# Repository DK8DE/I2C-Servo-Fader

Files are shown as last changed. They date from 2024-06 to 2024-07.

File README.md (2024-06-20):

# I2C-Servo-Fader 
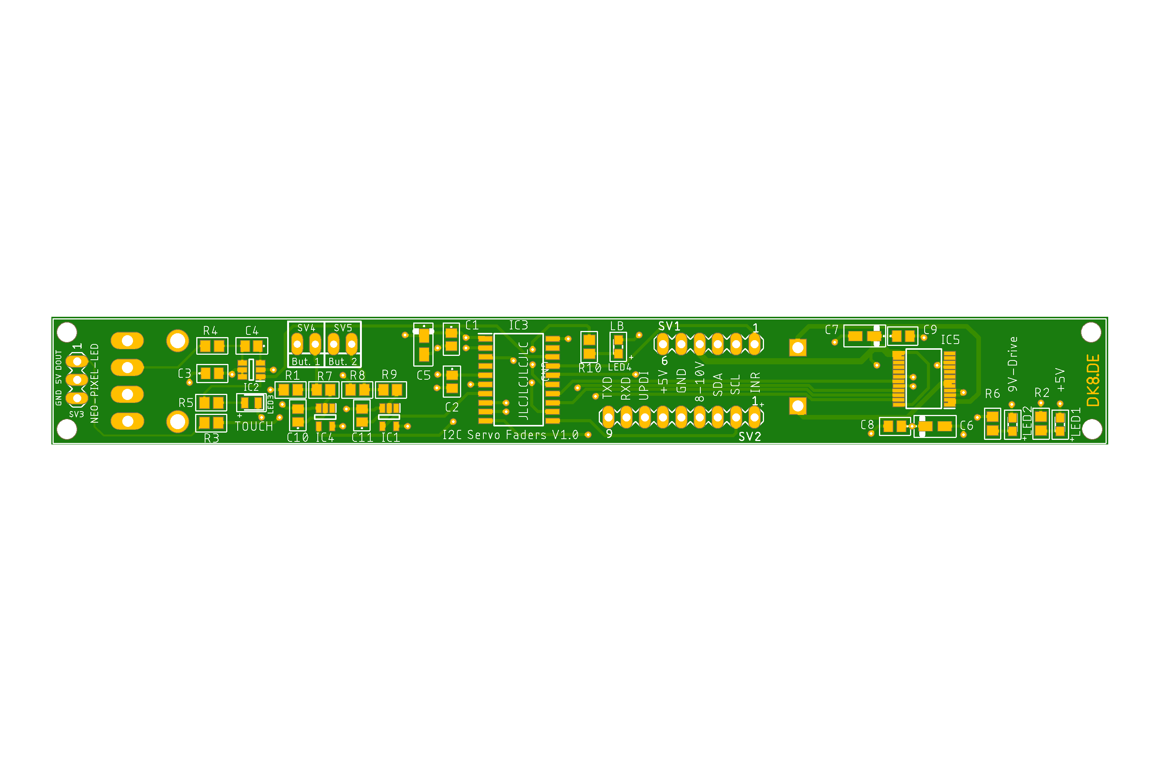
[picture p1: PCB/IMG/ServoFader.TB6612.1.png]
PCB

> [!CAUTION]
> The project is not yet complete. I am still waiting for the faders and the PCBs. Only then can I finish writing the code for the fader. The code still lacks the motor control in relation to the fader track.
## Description
This project consists of a board for a motor fader, the code for the microcontroller on the board, and a library to control this fader with an Arduino or an ESP32. The compatible faders are:
+ Behringer X-Touch Motor-Fader MF100T
+ Soundwell SM10001NKA0X-HA1
+ RSA0N11M9A07

Of course, the board can also be adapted for other faders by adjusting the footprint.

### Connections on the Board:
* SDA
* SCL
* +5V for the microcontroller
* 8-10V for the motor
* 1x interrupt pin
* 1x Opt button
* 1x Neo-Pixel-LED
* 1x UPDI

All signals are looped through on the board. This means that several boards can be placed next to each other and easily connected to each other.

## Funktion
The board also has the option to control a NeoPixel LED and an additional button. The NeoPixel LED can be fully controlled via the I2C bus, including RGB color, on, off, and brightness. This allows, for example, changing the color based on the set level or displaying notifications.
The fader has a touch function that can also be evaluated and is internally used to trigger an interrupt. You only need to check when the interrupt line is pulled LOW.
The optional button input can be queried and also triggers an interrupt when pressed.
The interrupt is only reset when the value on the fader that caused the interrupt is read. This ensures that no unnecessary queries are made and no changes are lost.
In the example code, the interrupt line is connected to a pin on the microcontroller that can also trigger an interrupt. This ensures that the microcontroller responds immediately to changes. On an Arduino UNO or Nano, pins 2 and 3 can be used.
To set an I2C address for the fader, you need to connect to the fader using the serial console and simply enter the address in the format 0x08. The address is then stored in ROM and used on the next startup. In theory, you can operate 127 faders on one bus ;-).
The functions of the library are thoroughly documented in I2cServoFader.h, and all functions are used in the example code. The example code also shows how to control multiple sliders.

# Example Code Description
This example code demonstrates how to control I2C servo sliders using an Arduino. The code supports one slider and can be extended to two sliders by uncommenting the relevant sections. The sliders can be controlled via serial commands, and their positions and LED colors can be adjusted based on analog values.

### Serial Commands:
+ sliderpos1=<value>: Sets the position of slider 1 to the specified value (0-255).
+ sliderpos2=<value>: Sets the position of slider 2 to the specified value (0-255).
+ slidertest=1: Initiates a demonstration of slider 1's movement through a series of positions.
+ slidertest=2: Initiates a demonstration of slider 2's movement through a series of positions.

### Interrupt Handling:
When an interrupt occurs, the code reads the analog value and optio state from the sliders, prints these values to the serial console, and updates the LED colors based on the analog values.
The interrupt is triggered by a change in the state of the connected pin (e.g., pin 2).

### LED Color Representation:
+ Green (analog value = 0)
+ Yellow (analog value ≈ 128)
+ Red (analog value = 255)
The LED color transitions smoothly between these values based on the analog value.
# Sources
Part of the circuit board layout is from this project:
https://github.com/GadgetReboot/PSM60_Fader_Controller

# Partlist
This is the BOM. If you don't buy the faders in Germany but from the friendly Chinese, they cost about 12€ per piece.
You can find them on AliExpress here: [RSA0N11M9A0J](https://de.aliexpress.com/item/1005006910254678.html).

| Part | Value | Package | PART_NUMBER | Price €|
|:--- |:--- |:--- |:--- |:--- |
| C1 | 100nF | C0805 | C0805C104K1RACTU | 0.16 | 
| C2 | 10nF | C0805 | C0805Y103K4RACTU | 0.16 |
| C3 | 100nF | C0805 | C0805C104K1RACTU | 0.16 |
| C4 | 22nF | C0805 | C0805C223K5RAC7210 | 0.09|
| C5 | 10uF | T491A | T491A106M016AT7280 | 0.35 |
| C6 | 10uF | T491A | T491A106M016AT7280 | 0.35 |
| C7 | 10uF | T491A | T491A106M016AT7280 | 0.35 |
| C8 | 100nF | C0805 | C0805C104K1RACTU | 0.16 |
| C9 | 100nF | C0805 | C0805C104K1RACTU | 0.16 |
| FADER | MF100T | SM10001NKA0X-HA1 |  | 20.00|
| IC1 | ATTINY1604-SSN | SOIC127P600X175-14N | ATTINY1604-SSN | 0.70|
| IC2 | AT42QT1010 | SOT95P280X145-6N | AT42QT1010-TSHR | 0.72|
| IC4 | SN74LVC1G14DBVR | SOT95P280X145-5N | SN74LVC1G14DBVR | 0.20 |
| IC5 | TB6612FNG,C,8,EL | SOP65P760X160-24N | TB6612FNG,C,8,EL | 1.35 |
| LED1 | 150080GS75000 | LEDM2012X80N | 150080GS75000 | 0.18 |
| LED2 | 150080GS75000 | LEDM2012X80N | 150080GS75000 | 0.18 |
| LED3 | 150080YS75000 | LEDC2012X80N | 150080YS75000 | 0.18 |
| R1 | 0R | R0805 | OPT | 0.08 |
| R2 | 1K | R0805 | | 0.08 |
| R3 | 470R | R0805 | | 0.08 | 
| R4 | 10K | R0805 | | 0.08 |
| R5 | 1K | R0805 | | 0.08 |
| R6 | 1K | R0805 | | 0.08 |
| SV1 | 0 | MA06-1 | | 0.15 |
| SV2 | 0 | MA06-1 | | 0.15 |
| SV3 | 0 | MA03-1 | | 0.15 |
| SV4 | 0 | MA03-1 | | 0.15 |
| SV5 | 22-23-2021 | 22-23-2021 | | 0.20 |
| PCB ||||2.00|
|T-Lever |||| 1.25 |
|Total |||| ~ 28.00€ |

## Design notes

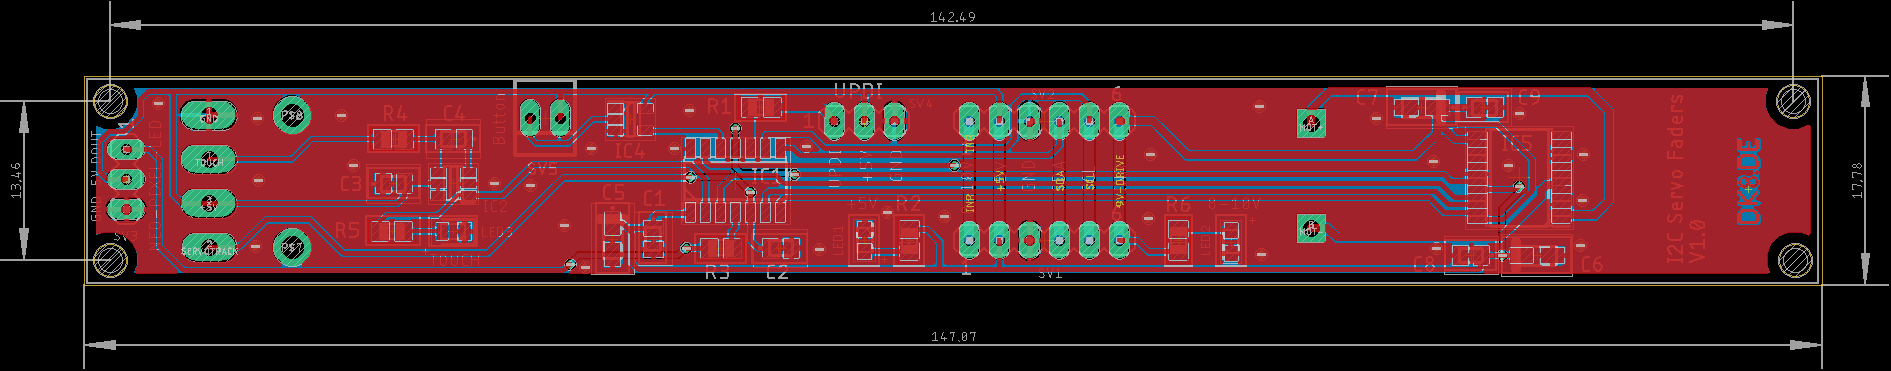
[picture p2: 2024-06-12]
PCB/IMG/ServoFader.TB6612.2.png

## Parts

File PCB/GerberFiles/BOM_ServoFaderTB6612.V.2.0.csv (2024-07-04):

Part | Value | Device | Package | Description | DESCRIPTION | HEIGHT | MANUFACTURER_NAME | MANUFACTURER_PART_NUMBER | MF | MOUSER_PART_NUMBER | MOUSER_PRICE-STOCK | MPN | OC_FARNELL | OC_NEWARK | POPULARITY | SPICEPREFIX
C1 | 100nF | C0805C104K1RACTU | C0805 | SMD Comm X7R, Ceramic, 0.1 uF, 10%, 100 VDC, 250 VDC, 125C, -55C, X7R, SMD, MLCC, Temperature Stable, Class II, 2.5 % , 10 GOhms, 16 mg, 0805, 2mm, 1.25mm, 1mm, 0.75mm, 0.5mm, 2500, 78 Weeks, 80 | SMD Comm X7R, Ceramic, 0.1 uF, 10%, 100 VDC, 250 VDC, 125C, -55C, X7R, SMD, MLCC, Temperature Stable, Class II, 2.5 % , 10 GOhms, 16 mg, 0805, 2mm, 1.25mm, 1mm, 0.75mm, 0.5mm, 2500, 78 Weeks, 80 | 1.1mm | KEMET | C0805C104K1RACTU |  | 80-C0805C104K1R | https://www.mouser.co.uk/ProductDetail/KEMET/C0805C104K1RACTU?qs=%252BnQd%252BVdkwTpk7hSy9esUqA%3D%3D
C2 | 10nF | C0805Y103K4RACTU | C0805 | SMD Comm X7R FF, Ceramic, 0.01 uF, 10%, 16 VDC, 40 VDC, 125C, -55C, X7R, SMD, MLCC, FF-CAP, Floating Electrode, 3.5 % , 100 GOhms, 13 mg, 0805, 2mm, 1.25mm, 0.78mm, 0.75mm, 0.5mm, 4000, 78 Weeks, 80 | SMD Comm X7R FF, Ceramic, 0.01 uF, 10%, 16 VDC, 40 VDC, 125C, -55C, X7R, SMD, MLCC, FF-CAP, Floating Electrode, 3.5 % , 100 GOhms, 13 mg, 0805, 2mm, 1.25mm, 0.78mm, 0.75mm, 0.5mm, 4000, 78 Weeks, 80 | 1.1mm | KEMET | C0805Y103K4RACTU |  | 80-C0805Y103K4R | https://www.mouser.co.uk/ProductDetail/KEMET/C0805Y103K4RACTU?qs=sbamQQFaV8yazvNwKcnfeQ%3D%3D
C3 | 100nF | C0805C223K5RAC7210 | C0805 | SMD Comm X7R, Ceramic, 0.022 uF, 10%, 50 VDC, 125 VDC, 125C, -55C, X7R, SMD, MLCC, Temperature Stable, Class II, 2.5 % , 45.4545 GOhms, 11 mg, 0805, 2mm, 1.25mm, 0.78mm, 0.75mm, 0.5mm, 15000, 78 Weeks, 80 | SMD Comm X7R, Ceramic, 0.022 uF, 10%, 50 VDC, 125 VDC, 125C, -55C, X7R, SMD, MLCC, Temperature Stable, Class II, 2.5 % , 45.4545 GOhms, 11 mg, 0805, 2mm, 1.25mm, 0.78mm, 0.75mm, 0.5mm, 15000, 78 Weeks, 80 | 1.1mm | KEMET | C0805C223K5RAC7210
C4 | 22nF | C0805C223K5RAC7210 | C0805 | SMD Comm X7R, Ceramic, 0.022 uF, 10%, 50 VDC, 125 VDC, 125C, -55C, X7R, SMD, MLCC, Temperature Stable, Class II, 2.5 % , 45.4545 GOhms, 11 mg, 0805, 2mm, 1.25mm, 0.78mm, 0.75mm, 0.5mm, 15000, 78 Weeks, 80 | SMD Comm X7R, Ceramic, 0.022 uF, 10%, 50 VDC, 125 VDC, 125C, -55C, X7R, SMD, MLCC, Temperature Stable, Class II, 2.5 % , 45.4545 GOhms, 11 mg, 0805, 2mm, 1.25mm, 0.78mm, 0.75mm, 0.5mm, 15000, 78 Weeks, 80 | 1.1mm | KEMET | C0805C223K5RAC7210
C5 | 10uF | T491A106M016AT7280 | T491A | T491, Tantalum, MnO2 Tantalum, Commercial Grade, 10 uF, 20%, 16 VDC, 125C, -55C, 85C, SMD, MnO2, Molded, 6 % , 3 Ohms, 1600 nA, 58.6 mg, 3216, 1.6mm, Height Max = 1.8mm, 9000, 156 Weeks | T491, Tantalum, MnO2 Tantalum, Commercial Grade, 10 uF, 20%, 16 VDC, 125C, -55C, 85C, SMD, MnO2, Molded, 6 % , 3 Ohms, 1600 nA, 58.6 mg, 3216, 1.6mm, Height Max = 1.8mm, 9000, 156 Weeks | 1.8mm | KEMET | T491A106M016AT7280 |  | 80-T491A106M16AT7280 | https://www.mouser.co.uk/ProductDetail/KEMET/T491A106M016AT7280?qs=WOKUqv%2F%2FT%2FbXhYcv8zpvIg%3D%3D
C6 | 10uF | T491A106M016AT7280 | T491A | T491, Tantalum, MnO2 Tantalum, Commercial Grade, 10 uF, 20%, 16 VDC, 125C, -55C, 85C, SMD, MnO2, Molded, 6 % , 3 Ohms, 1600 nA, 58.6 mg, 3216, 1.6mm, Height Max = 1.8mm, 9000, 156 Weeks | T491, Tantalum, MnO2 Tantalum, Commercial Grade, 10 uF, 20%, 16 VDC, 125C, -55C, 85C, SMD, MnO2, Molded, 6 % , 3 Ohms, 1600 nA, 58.6 mg, 3216, 1.6mm, Height Max = 1.8mm, 9000, 156 Weeks | 1.8mm | KEMET | T491A106M016AT7280 |  | 80-T491A106M16AT7280 | https://www.mouser.co.uk/ProductDetail/KEMET/T491A106M016AT7280?qs=WOKUqv%2F%2FT%2FbXhYcv8zpvIg%3D%3D
C7 | 10uF | T491A106M016AT7280 | T491A | T491, Tantalum, MnO2 Tantalum, Commercial Grade, 10 uF, 20%, 16 VDC, 125C, -55C, 85C, SMD, MnO2, Molded, 6 % , 3 Ohms, 1600 nA, 58.6 mg, 3216, 1.6mm, Height Max = 1.8mm, 9000, 156 Weeks | T491, Tantalum, MnO2 Tantalum, Commercial Grade, 10 uF, 20%, 16 VDC, 125C, -55C, 85C, SMD, MnO2, Molded, 6 % , 3 Ohms, 1600 nA, 58.6 mg, 3216, 1.6mm, Height Max = 1.8mm, 9000, 156 Weeks | 1.8mm | KEMET | T491A106M016AT7280 |  | 80-T491A106M16AT7280 | https://www.mouser.co.uk/ProductDetail/KEMET/T491A106M016AT7280?qs=WOKUqv%2F%2FT%2FbXhYcv8zpvIg%3D%3D
C8 | 100nF | C0805C104K1RACTU | C0805 | SMD Comm X7R, Ceramic, 0.1 uF, 10%, 100 VDC, 250 VDC, 125C, -55C, X7R, SMD, MLCC, Temperature Stable, Class II, 2.5 % , 10 GOhms, 16 mg, 0805, 2mm, 1.25mm, 1mm, 0.75mm, 0.5mm, 2500, 78 Weeks, 80 | SMD Comm X7R, Ceramic, 0.1 uF, 10%, 100 VDC, 250 VDC, 125C, -55C, X7R, SMD, MLCC, Temperature Stable, Class II, 2.5 % , 10 GOhms, 16 mg, 0805, 2mm, 1.25mm, 1mm, 0.75mm, 0.5mm, 2500, 78 Weeks, 80 | 1.1mm | KEMET | C0805C104K1RACTU |  | 80-C0805C104K1R | https://www.mouser.co.uk/ProductDetail/KEMET/C0805C104K1RACTU?qs=%252BnQd%252BVdkwTpk7hSy9esUqA%3D%3D
C9 | 100nF | C0805C104K1RACTU | C0805 | SMD Comm X7R, Ceramic, 0.1 uF, 10%, 100 VDC, 250 VDC, 125C, -55C, X7R, SMD, MLCC, Temperature Stable, Class II, 2.5 % , 10 GOhms, 16 mg, 0805, 2mm, 1.25mm, 1mm, 0.75mm, 0.5mm, 2500, 78 Weeks, 80 | SMD Comm X7R, Ceramic, 0.1 uF, 10%, 100 VDC, 250 VDC, 125C, -55C, X7R, SMD, MLCC, Temperature Stable, Class II, 2.5 % , 10 GOhms, 16 mg, 0805, 2mm, 1.25mm, 1mm, 0.75mm, 0.5mm, 2500, 78 Weeks, 80 | 1.1mm | KEMET | C0805C104K1RACTU |  | 80-C0805C104K1R | https://www.mouser.co.uk/ProductDetail/KEMET/C0805C104K1RACTU?qs=%252BnQd%252BVdkwTpk7hSy9esUqA%3D%3D
C10 | 100nF | C0805C104K1RACTU | C0805 | SMD Comm X7R, Ceramic, 0.1 uF, 10%, 100 VDC, 250 VDC, 125C, -55C, X7R, SMD, MLCC, Temperature Stable, Class II, 2.5 % , 10 GOhms, 16 mg, 0805, 2mm, 1.25mm, 1mm, 0.75mm, 0.5mm, 2500, 78 Weeks, 80 | SMD Comm X7R, Ceramic, 0.1 uF, 10%, 100 VDC, 250 VDC, 125C, -55C, X7R, SMD, MLCC, Temperature Stable, Class II, 2.5 % , 10 GOhms, 16 mg, 0805, 2mm, 1.25mm, 1mm, 0.75mm, 0.5mm, 2500, 78 Weeks, 80 | 1.1mm | KEMET | C0805C104K1RACTU |  | 80-C0805C104K1R | https://www.mouser.co.uk/ProductDetail/KEMET/C0805C104K1RACTU?qs=%252BnQd%252BVdkwTpk7hSy9esUqA%3D%3D
C11 | 100nF | C0805C104K1RACTU | C0805 | SMD Comm X7R, Ceramic, 0.1 uF, 10%, 100 VDC, 250 VDC, 125C, -55C, X7R, SMD, MLCC, Temperature Stable, Class II, 2.5 % , 10 GOhms, 16 mg, 0805, 2mm, 1.25mm, 1mm, 0.75mm, 0.5mm, 2500, 78 Weeks, 80 | SMD Comm X7R, Ceramic, 0.1 uF, 10%, 100 VDC, 250 VDC, 125C, -55C, X7R, SMD, MLCC, Temperature Stable, Class II, 2.5 % , 10 GOhms, 16 mg, 0805, 2mm, 1.25mm, 1mm, 0.75mm, 0.5mm, 2500, 78 Weeks, 80 | 1.1mm | KEMET | C0805C104K1RACTU |  | 80-C0805C104K1R | https://www.mouser.co.uk/ProductDetail/KEMET/C0805C104K1RACTU?qs=%252BnQd%252BVdkwTpk7hSy9esUqA%3D%3D
FADER | MF100T | SM10001NKA0X-HA1 | SM10001NKA0X-HA1 | Behringer X-Touch Motor-Fader MF100T
IC1 | SN74LVC1G14DBVR | SN74LVC1G14DBVR | SOT95P280X145-5N | TEXAS INSTRUMENTS - SN74LVC1G14DBVR - IC, SCHMITT TRIGGER INVERTER, SMD | TEXAS INSTRUMENTS - SN74LVC1G14DBVR - IC, SCHMITT TRIGGER INVERTER, SMD | 1.45mm | Texas Instruments | SN74LVC1G14DBVR |  | 595-SN74LVC1G14DBVR | https://www.mouser.co.uk/ProductDetail/Texas-Instruments/SN74LVC1G14DBVR?qs=dT9u2OTAaVWRIgCrQFnxuQ%3D%3D
IC2 | AT42QT1010 | AT42QT1010-TSHR | SOT95P280X145-6N | AT42QT1010-TSHR, Spread-Spectrum Charge-Transfer Touch Screen Controller, 14 bit, 6-Pin SOT-23 | AT42QT1010-TSHR, Spread-Spectrum Charge-Transfer Touch Screen Controller, 14 bit, 6-Pin SOT-23 | 1.45mm | Microchip | AT42QT1010-TSHR |  | 556-AT42QT1010-TSHR | https://www.mouser.co.uk/ProductDetail/Microchip-Technology/AT42QT1010-TSHR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
IC3 | ATTINY1616-SNR | ATTINY1616-SNR | SOIC127P1030X265-20N | 8-bit Microcontrollers - MCU 20MHZ SOIC 85C GRN | 8-bit Microcontrollers - MCU 20MHZ SOIC 85C GRN | 2.65mm | Microchip | ATTINY1616-SNR |  | 556-ATTINY1616SNR | https://www.mouser.co.uk/ProductDetail/Microchip-Technology-Atmel/ATTINY1616-SNR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
IC4 | SN74LVC1G14DBVR | SN74LVC1G14DBVR | SOT95P280X145-5N | TEXAS INSTRUMENTS - SN74LVC1G14DBVR - IC, SCHMITT TRIGGER INVERTER, SMD | TEXAS INSTRUMENTS - SN74LVC1G14DBVR - IC, SCHMITT TRIGGER INVERTER, SMD | 1.45mm | Texas Instruments | SN74LVC1G14DBVR |  | 595-SN74LVC1G14DBVR | https://www.mouser.co.uk/ProductDetail/Texas-Instruments/SN74LVC1G14DBVR?qs=dT9u2OTAaVWRIgCrQFnxuQ%3D%3D
IC5 | TB6612FNG,C,8,EL | TB6612FNG,C,8,EL | SOP65P760X160-24N | otor / Motion / Ignition Controllers & Drivers Brush Motor Driver IC | otor / Motion / Ignition Controllers & Drivers Brush Motor Driver IC | 1.6mm | Toshiba | TB6612FNG,C,8,EL |  | 757-TB6612FNGC8EL | https://www.mouser.co.uk/ProductDetail/Toshiba/TB6612FNGC8EL?qs=rsevcuukUAy2UalRuv4E%2FQ%3D%3D
LED1 | 150080GS75000 | 150080GS75000 | LEDM2012X80N | 150080GS75000, Wurth Elektronik WL-SMCW 520 nm Green LED, 2012 (0805) Clear SMD package | 150080GS75000, Wurth Elektronik WL-SMCW 520 nm Green LED, 2012 (0805) Clear SMD package | 0.8mm | Wurth Elektronik | 150080GS75000 |  | 710-150080GS75000 | https://www.mouser.co.uk/ProductDetail/Wurth-Elektronik/150080GS75000?qs=2kOmHSv6VfQRoTEZVk1mGA%3D%3D
LED2 | 150080GS75000 | 150080GS75000 | LEDM2012X80N | 150080GS75000, Wurth Elektronik WL-SMCW 520 nm Green LED, 2012 (0805) Clear SMD package | 150080GS75000, Wurth Elektronik WL-SMCW 520 nm Green LED, 2012 (0805) Clear SMD package | 0.8mm | Wurth Elektronik | 150080GS75000 |  | 710-150080GS75000 | https://www.mouser.co.uk/ProductDetail/Wurth-Elektronik/150080GS75000?qs=2kOmHSv6VfQRoTEZVk1mGA%3D%3D
LED3 | 150080YS75000 | 150080YS75000 | LEDC2012X80N | LED,Wurth Elektronik,150080YS75000 | LED,Wurth Elektronik,150080YS75000 | 0.8mm | Wurth Elektronik | 150080YS75000 |  | 710-150080YS75000 | https://www.mouser.co.uk/ProductDetail/Wurth-Elektronik/150080YS75000?qs=LlUlMxKIyB3k0fZGrDMI2w%3D%3D
LED4 | 150080GS75000 | 150080GS75000 | LEDM2012X80N | 150080GS75000, Wurth Elektronik WL-SMCW 520 nm Green LED, 2012 (0805) Clear SMD package | 150080GS75000, Wurth Elektronik WL-SMCW 520 nm Green LED, 2012 (0805) Clear SMD package | 0.8mm | Wurth Elektronik | 150080GS75000 |  | 710-150080GS75000 | https://www.mouser.co.uk/ProductDetail/Wurth-Elektronik/150080GS75000?qs=2kOmHSv6VfQRoTEZVk1mGA%3D%3D
LOGO | DK8DESS | DK8DESS | DK8DE_KLEIN
R1 | 100K | R-EU_R0805 | R0805 | RESISTOR, European symbol |  |  |  |  |  |  |  |  |  |  | 86 | R
R2 | 1K | R-EU_R0805 | R0805 | RESISTOR, European symbol |  |  |  |  |  |  |  |  |  |  | 86 | R
R3 | 470R | R-EU_R0805 | R0805 | RESISTOR, European symbol |  |  |  |  |  |  |  |  |  |  | 86 | R
R4 | 10K | R-EU_R0805 | R0805 | RESISTOR, European symbol |  |  |  |  |  |  |  |  |  |  | 86 | R
R5 | 1K | R-EU_R0805 | R0805 | RESISTOR, European symbol |  |  |  |  |  |  |  |  |  |  | 86 | R
R6 | 1K | R-EU_R0805 | R0805 | RESISTOR, European symbol |  |  |  |  |  |  |  |  |  |  | 86 | R
R7 | 100K | R-EU_R0805 | R0805 | RESISTOR, European symbol |  |  |  |  |  |  |  |  |  |  | 86 | R
R8 | 100K | R-EU_R0805 | R0805 | RESISTOR, European symbol |  |  |  |  |  |  |  |  |  |  | 86 | R
R9 | 100K | R-EU_R0805 | R0805 | RESISTOR, European symbol |  |  |  |  |  |  |  |  |  |  | 86 | R
R10 | 1K | R-EU_R0805 | R0805 | RESISTOR, European symbol |  |  |  |  |  |  |  |  |  |  | 86 | R
SV1 |  | MA06-1 | MA06-1 | PIN HEADER |  |  |  |  |  |  |  |  | unknown | unknown | 28
SV2 |  | MA09-1 | MA09-1 | PIN HEADER |  |  |  |  |  |  |  |  | unknown | unknown | 0
SV3 | 0 | MA03-1 | MA03-1 | PIN HEADER |  |  |  |  |  |  |  |  | unknown | unknown | 48
SV4 | 22-23-2021 | 22-23-2021 | 22-23-2021 | .100 (2.54mm) Center Header - 2 Pin" |  |  |  |  | MOLEX |  |  | 22-23-2021 | 1462926 | 25C3832 | 40
SV5 | 22-23-2021 | 22-23-2021 | 22-23-2021 | .100 (2.54mm) Center Header - 2 Pin" |  |  |  |  | MOLEX |  |  | 22-23-2021 | 1462926 | 25C3832 | 40

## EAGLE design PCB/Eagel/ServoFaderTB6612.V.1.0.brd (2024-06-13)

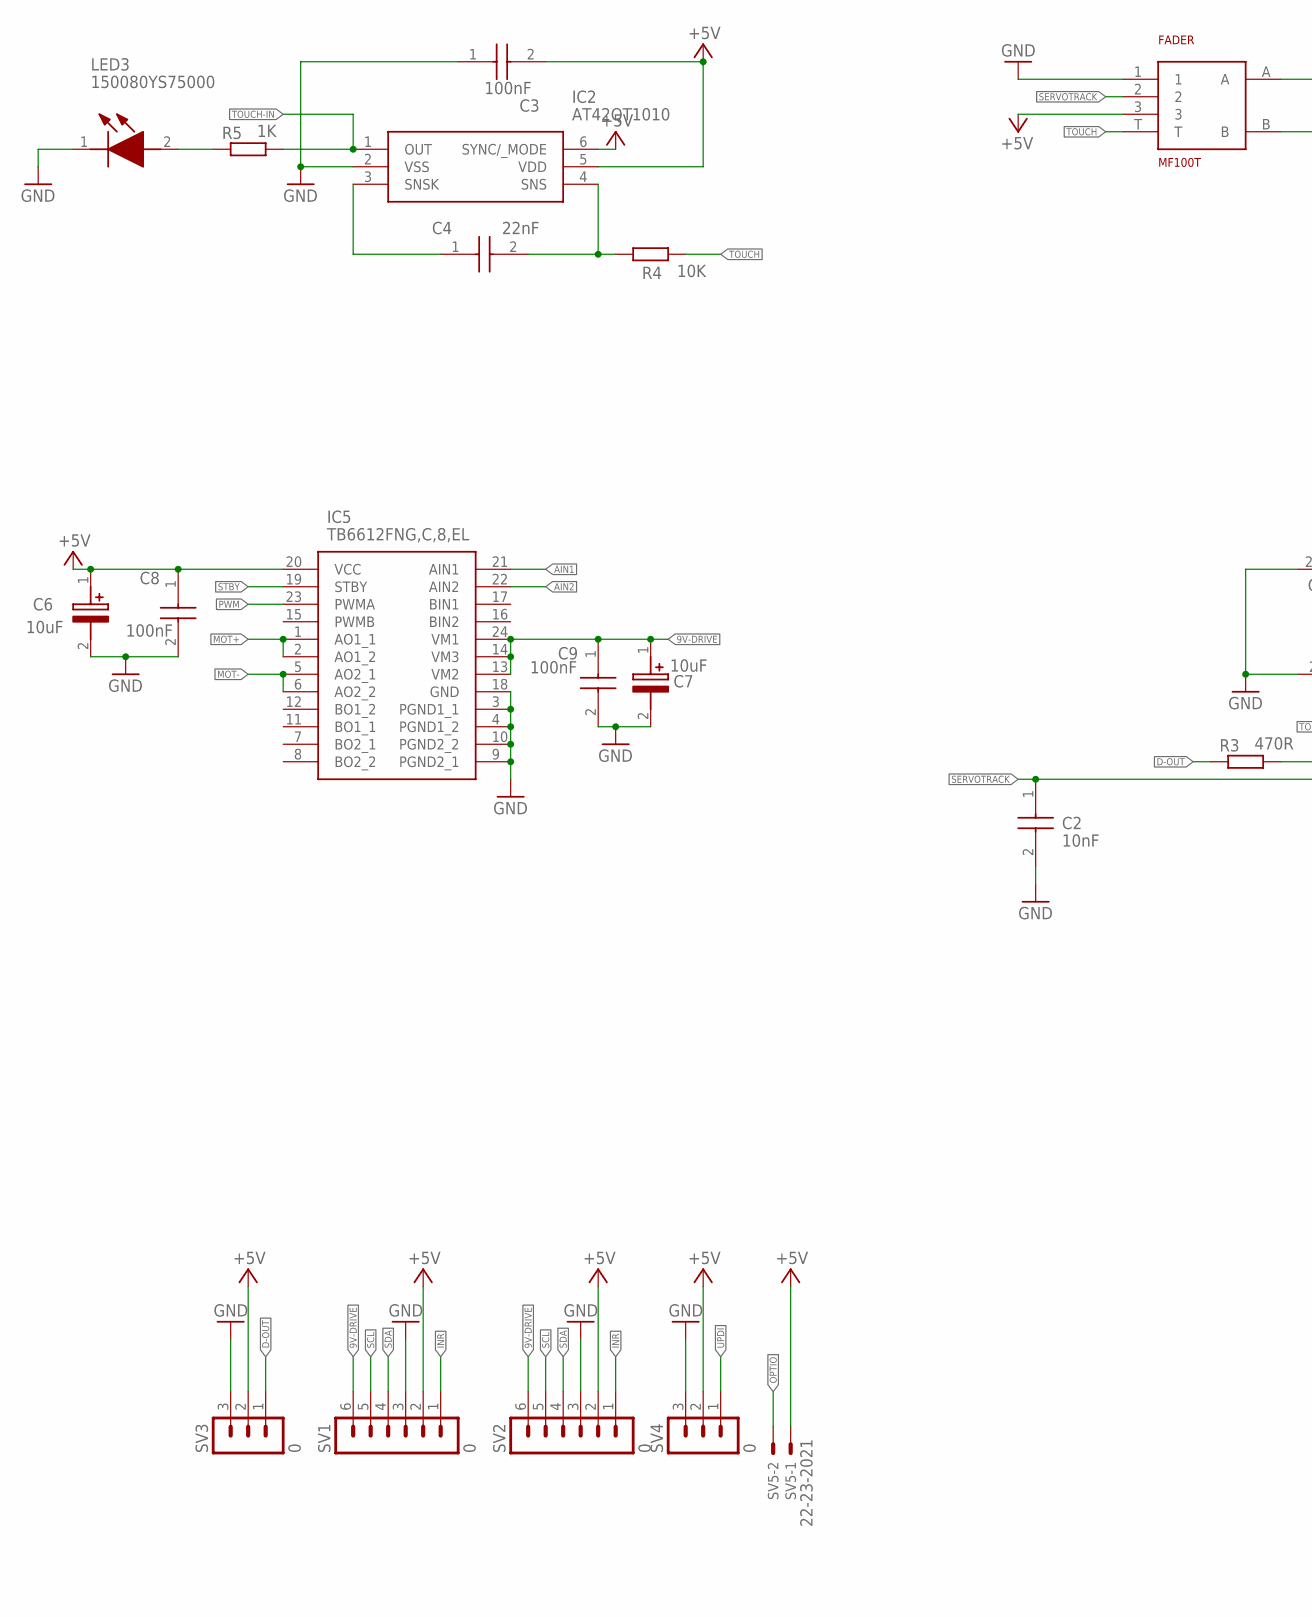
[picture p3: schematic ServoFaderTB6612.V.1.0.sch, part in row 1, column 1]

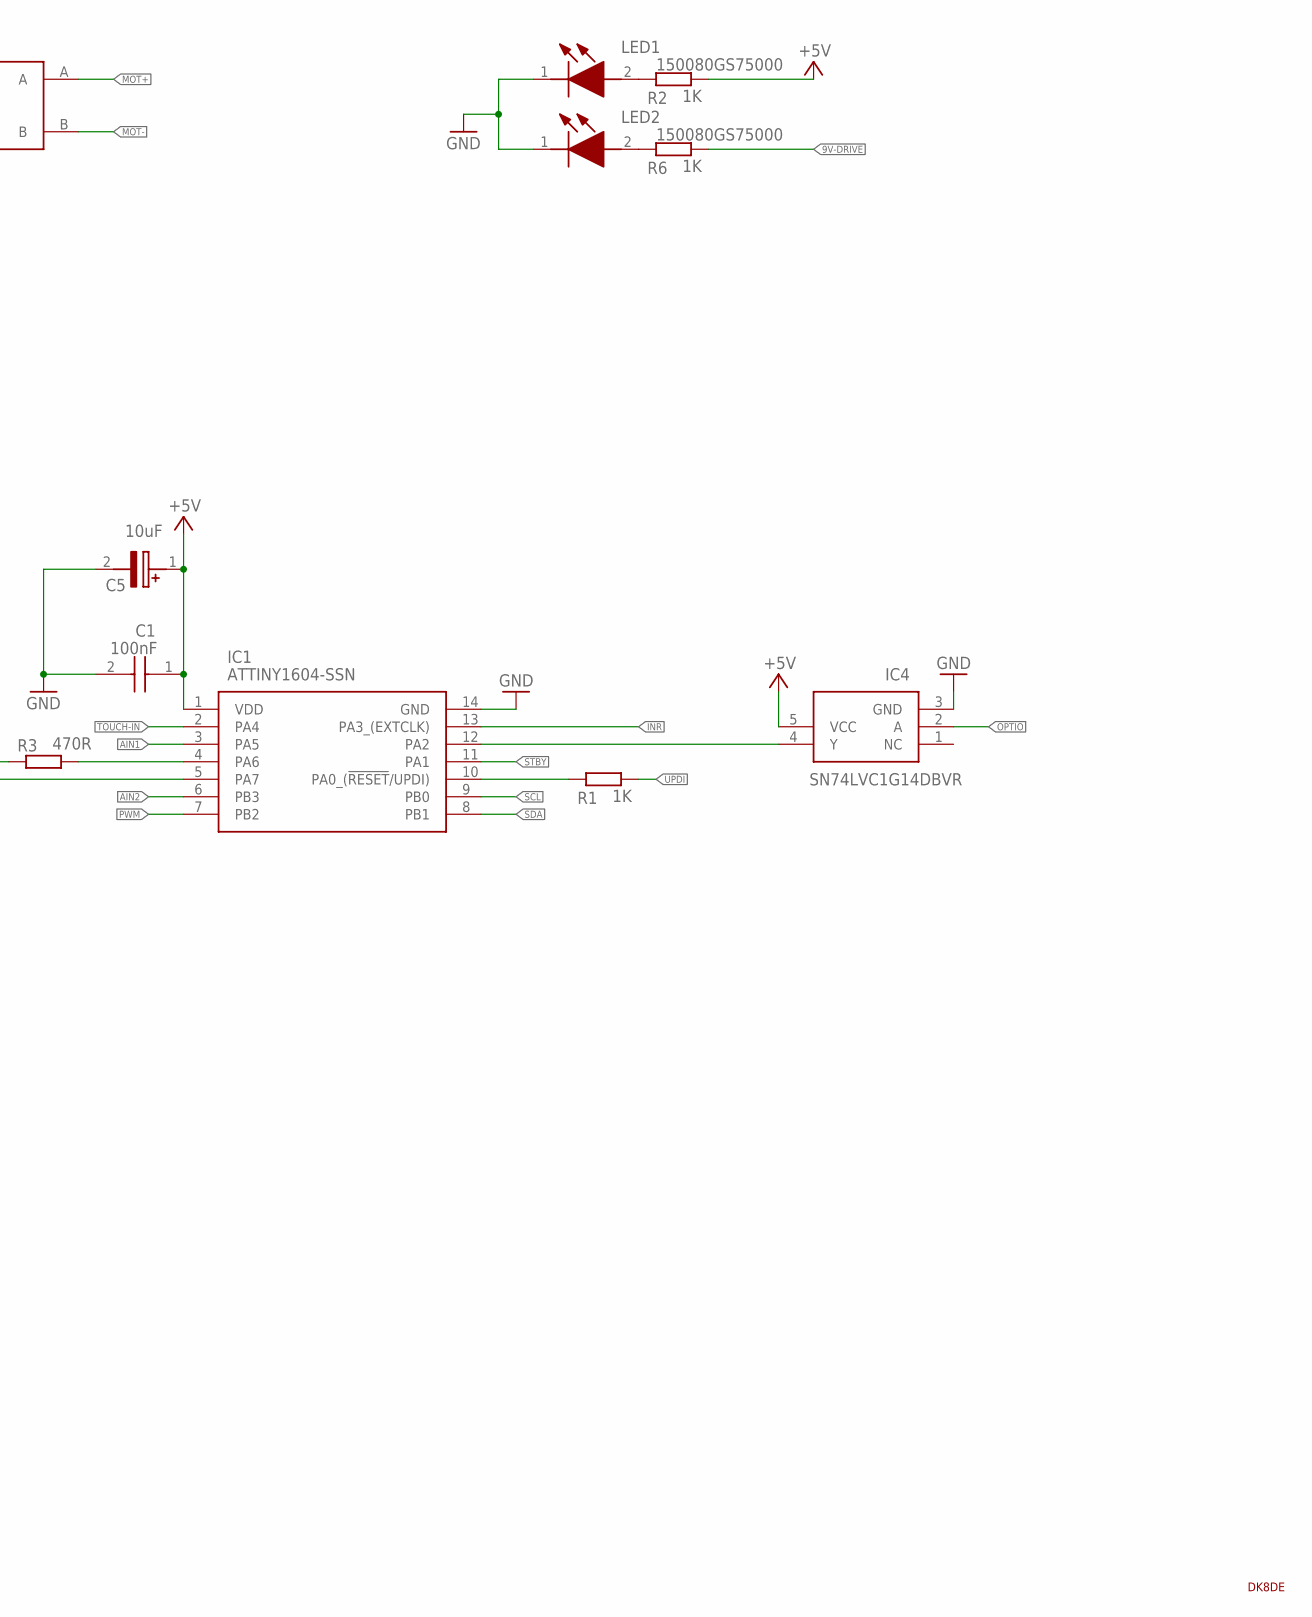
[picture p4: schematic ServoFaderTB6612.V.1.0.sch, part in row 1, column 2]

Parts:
C1, C3, C8, C9: 100nF; C0805
C2: 10nF; C0805
C4: 22nF; C0805
C5, C6, C7: 10uF; T491A
FADER: MF100T; SM10001NKA0X-HA1
IC1: ATTINY1604-SSN; SOIC127P600X175-14N
IC2: AT42QT1010; SOT95P280X145-6N
IC4: SN74LVC1G14DBVR; SOT95P280X145-5N
IC5: TB6612FNG,C,8,EL; SOP65P760X160-24N
LED1, LED2: 150080GS75000; LEDM2012X80N
LED3: 150080YS75000; LEDC2012X80N
LOGO: DK8DESS; DK8DE_KLEIN
R1, R2, R5, R6: 1K; R0805
R3: 470R; R0805
R4: 10K; R0805
SV1, SV2: 0; MA06-1
SV3, SV4: 0; MA03-1
SV5: 22-23-2021

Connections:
9V-DRIVE: C7.1 (+), C9.1, IC5.13 (VM2), IC5.14 (VM3), IC5.24 (VM1), R6.2, SV1.6, SV2.6
+5V: C1.1, C3.2, C5.1 (+), C6.1 (+), C8.1, FADER.3, IC1.1 (VDD), IC2.5 (VDD), IC2.6 (SYNC/_MODE), IC4.5 (VCC), IC5.20 (VCC), R2.2, SV1.2, SV2.2, SV3.2, SV4.2, SV5.1
AIN1: IC1.3 (PA5), IC5.21 (AIN1)
AIN2: IC1.6 (PB3), IC5.22 (AIN2)
D-OUT: R3.1, SV3.1
GND: C1.2, C2.2, C3.1, C5.2 (-), C6.2 (-), C7.2 (-), C8.2, C9.2, FADER.1, IC1.14 (GND), IC2.2 (VSS), IC4.3 (GND), IC5.3 (PGND1_1), IC5.4 (PGND1_2), IC5.9 (PGND2_1), IC5.10 (PGND2_2), IC5.18 (GND), LED1.1 (K), LED2.1 (K), LED3.1 (K), SV1.3, SV2.3, SV3.3, SV4.3
INR: IC1.13 (PA3_(EXTCLK)), SV1.1, SV2.1
MOT+: FADER.A, IC5.1 (AO1_1), IC5.2 (AO1_2)
MOT-: FADER.B, IC5.5 (AO2_1), IC5.6 (AO2_2)
unnamed: IC1.10 (PA0_(!RESET!/UPDI)), R1.1
unnamed: LED1.2 (A), R2.1
unnamed: LED2.2 (A), R6.1
unnamed: IC1.12 (PA2), IC4.4 (Y)
unnamed: IC1.4 (PA6), R3.2
unnamed: C4.1, IC2.3 (SNSK)
unnamed: C4.2, IC2.4 (SNS), R4.1
unnamed: LED3.2 (A), R5.1
OPTIO: IC4.2 (A), SV5.2
PWM: IC1.7 (PB2), IC5.23 (PWMA)
SCL: IC1.9 (PB0), SV1.5, SV2.5
SDA: IC1.8 (PB1), SV1.4, SV2.4
SERVOTRACK: C2.1, FADER.2, IC1.5 (PA7)
STBY: IC1.11 (PA1), IC5.19 (STBY)
TOUCH: FADER.T, R4.2
TOUCH-IN: IC1.2 (PA4), IC2.1 (OUT), R5.2
UPDI: R1.2, SV4.1

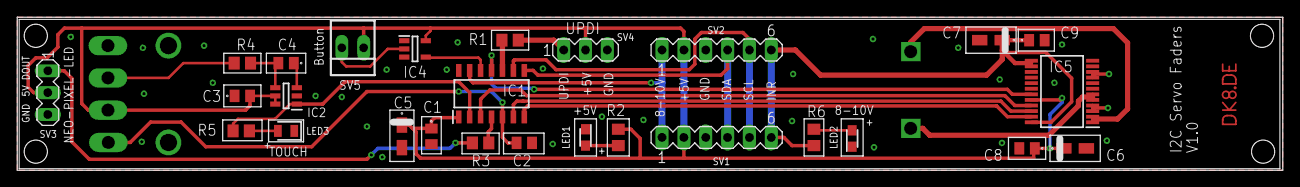
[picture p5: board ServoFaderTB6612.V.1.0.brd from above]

Board: 2 copper layers, 147.1 x 17.8 mm, 29 parts (0 on the bottom side), 26 nets.

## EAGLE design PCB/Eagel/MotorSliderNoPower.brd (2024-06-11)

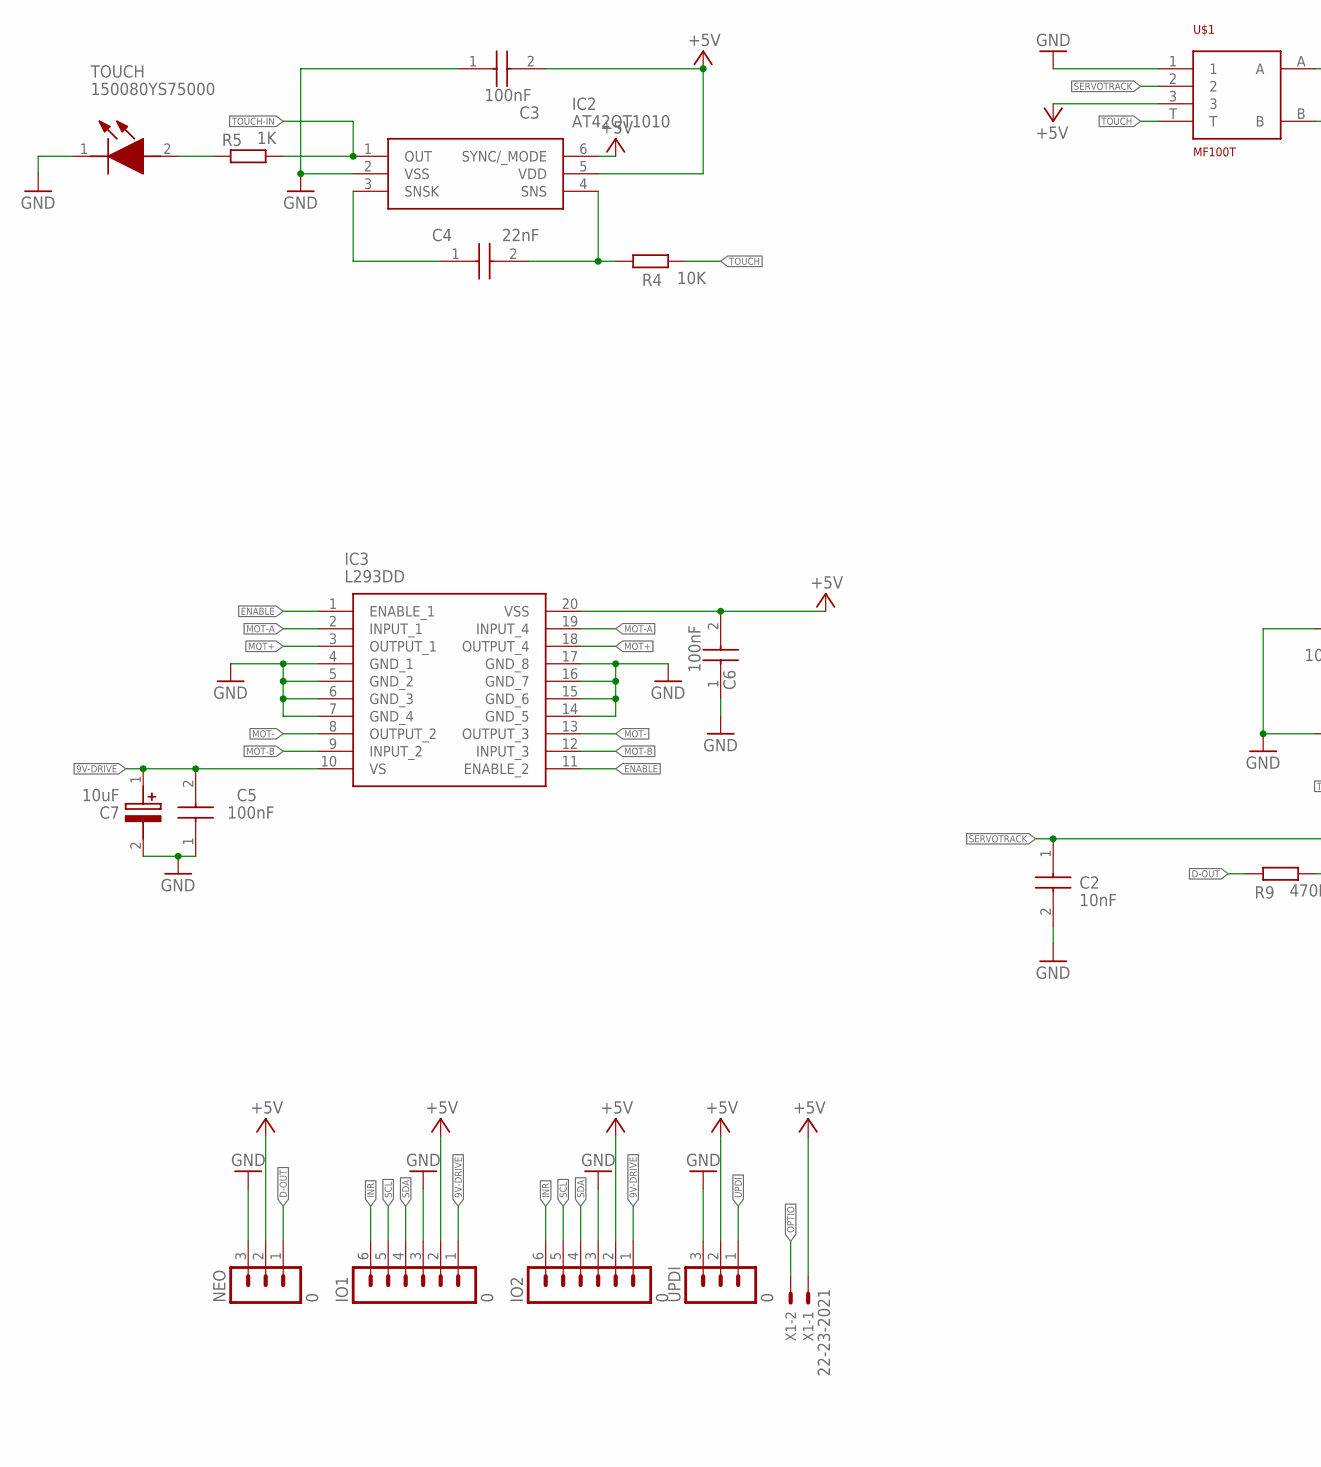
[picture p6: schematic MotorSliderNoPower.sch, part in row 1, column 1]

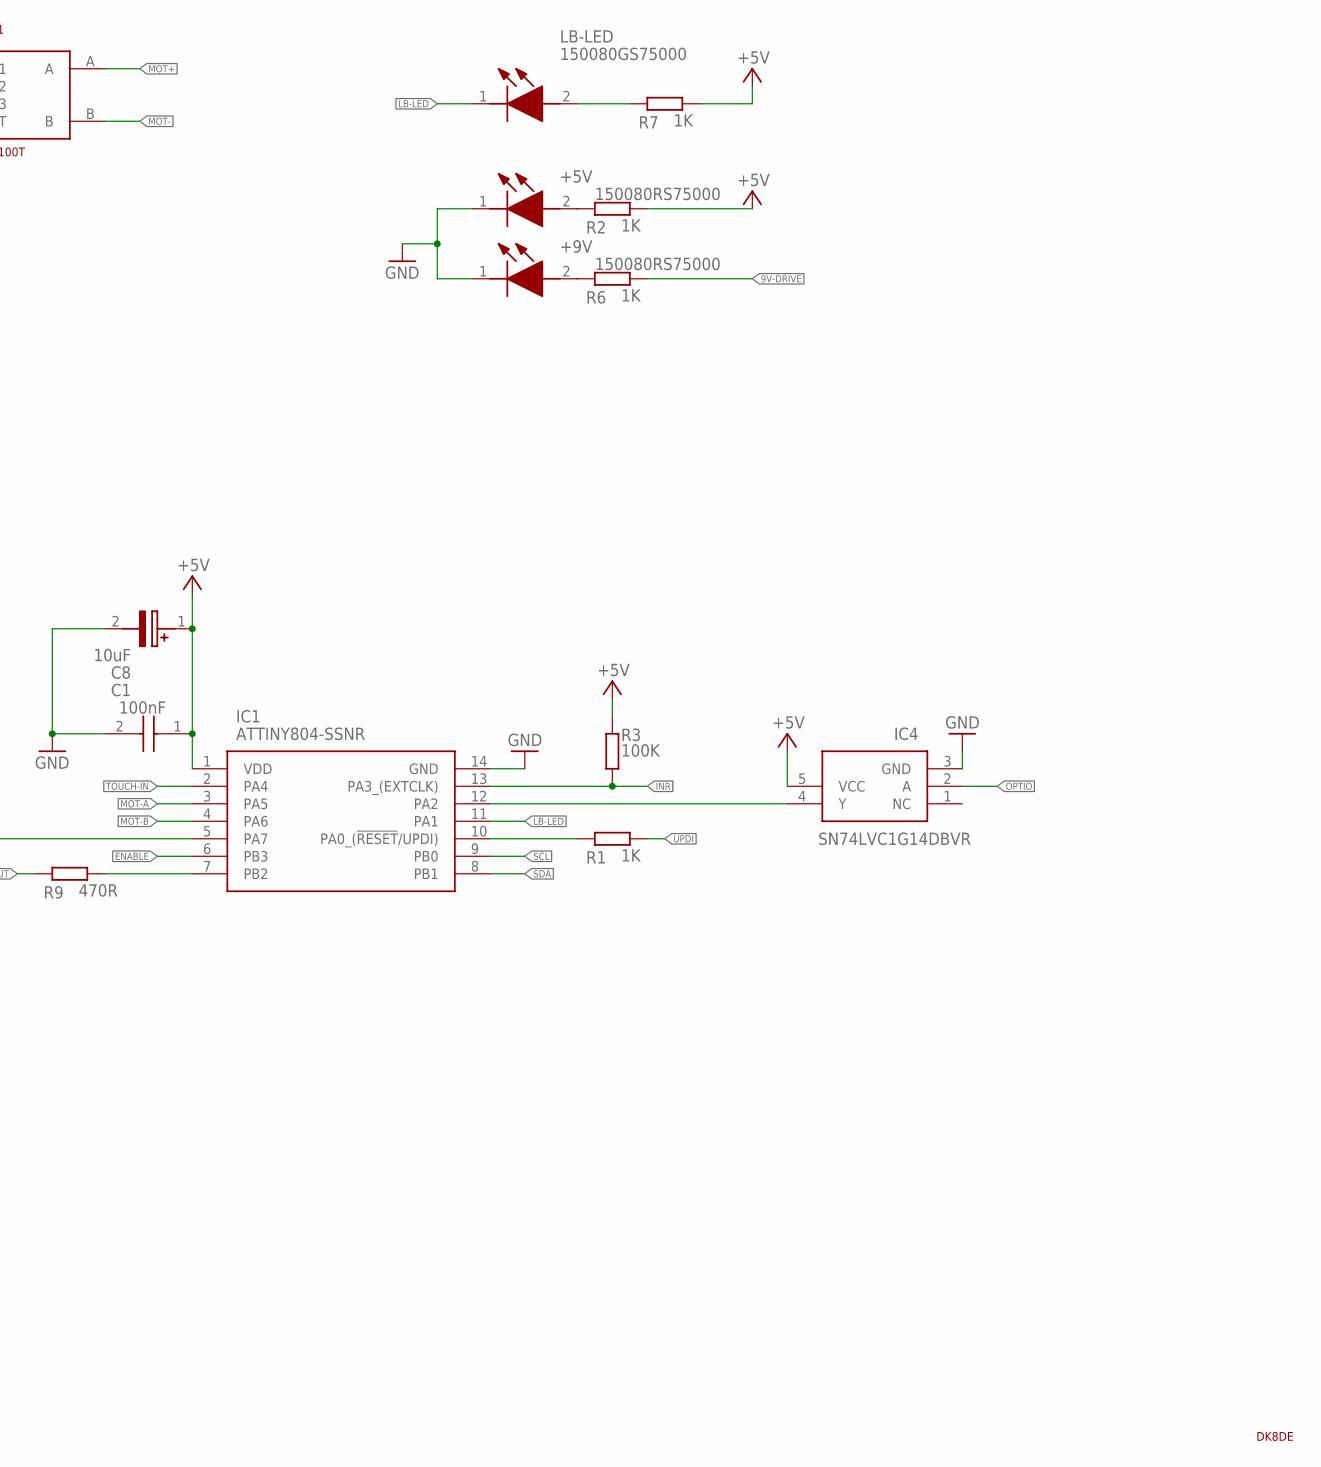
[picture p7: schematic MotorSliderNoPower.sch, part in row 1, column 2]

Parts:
+5V, +9V: 150080RS75000; LEDC2012X80N
C1, C3, C5, C6: 100nF; C0805
C2: 10nF; C0805
C4: 22nF; C0805
C7, C8: 10uF; EEE1AA220WR
IC1: ATTINY804-SSNR; SOIC127P600X175-14N
IC2: AT42QT1010; SOT95P280X145-6N
IC3: L293DD; SOIC127P1032X265-20N
IC4: SN74LVC1G14DBVR; SOT95P280X145-5N
IO1, IO2: 0; MA06-1
LB-LED: 150080GS75000; LEDM2012X80N
NEO: 0; MA03-1
R1, R2, R5, R6, R7: 1K; R0805
R3: 100K; R0805
R4: 10K; R0805
R9: 470R; R0805
TOUCH: 150080YS75000; LEDC2012X80N
U$1: MF100T; SM10001NKA0X-HA1
U$2: DK8DESS; DK8DE_KLEIN
UPDI: 0; MA03-1
X1: 22-23-2021

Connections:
9V-DRIVE: C5.2, C7.1 (+), IC3.10 (VS), IO1.1, IO2.1, R6.2
+5V: C1.1, C3.2, C6.2, C8.1 (+), IC1.1 (VDD), IC2.5 (VDD), IC2.6 (SYNC/_MODE), IC3.20 (VSS), IC4.5 (VCC), IO1.2, IO2.2, NEO.2, R2.2, R3.1, R7.2, U$1.3, UPDI.2, X1.1
D-OUT: NEO.1, R9.1
ENABLE: IC1.6 (PB3), IC3.1 (ENABLE_1), IC3.11 (ENABLE_2)
GND: +5V.1 (K), +9V.1 (K), C1.2, C2.2, C3.1, C5.1, C6.1, C7.2 (-), C8.2 (-), IC1.14 (GND), IC2.2 (VSS), IC3.4 (GND_1), IC3.5 (GND_2), IC3.6 (GND_3), IC3.7 (GND_4), IC3.14 (GND_5), IC3.15 (GND_6), IC3.16 (GND_7), IC3.17 (GND_8), IC4.3 (GND), IO1.3, IO2.3, NEO.3, TOUCH.1 (K), U$1.1, UPDI.3
INR: IC1.13 (PA3_(EXTCLK)), IO1.6, IO2.6, R3.2
LB-LED: IC1.11 (PA1), LB-LED.1 (K)
MOT+: IC3.3 (OUTPUT_1), IC3.18 (OUTPUT_4), U$1.A
MOT-: IC3.8 (OUTPUT_2), IC3.13 (OUTPUT_3), U$1.B
MOT-A: IC1.3 (PA5), IC3.2 (INPUT_1), IC3.19 (INPUT_4)
MOT-B: IC1.4 (PA6), IC3.9 (INPUT_2), IC3.12 (INPUT_3)
unnamed: IC1.10 (PA0_(!RESET!/UPDI)), R1.1
unnamed: +5V.2 (A), R2.1
unnamed: +9V.2 (A), R6.1
unnamed: IC1.12 (PA2), IC4.4 (Y)
unnamed: LB-LED.2 (A), R7.1
unnamed: IC1.7 (PB2), R9.2
unnamed: C4.1, IC2.3 (SNSK)
unnamed: C4.2, IC2.4 (SNS), R4.1
unnamed: R5.1, TOUCH.2 (A)
OPTIO: IC4.2 (A), X1.2
SCL: IC1.9 (PB0), IO1.5, IO2.5
SDA: IC1.8 (PB1), IO1.4, IO2.4
SERVOTRACK: C2.1, IC1.5 (PA7), U$1.2
TOUCH: R4.2, U$1.T
TOUCH-IN: IC1.2 (PA4), IC2.1 (OUT), R5.2
UPDI: R1.2, UPDI.1

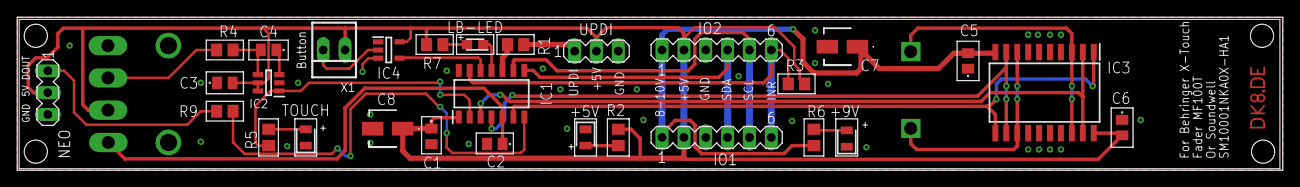
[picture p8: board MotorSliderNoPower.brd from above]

Board: 2 copper layers, 147.1 x 17.8 mm, 31 parts (0 on the bottom side), 27 nets.

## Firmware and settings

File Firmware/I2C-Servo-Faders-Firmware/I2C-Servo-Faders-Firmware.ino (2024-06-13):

#include <Wire.h>
#include <Adafruit_NeoPixel.h>
#include <EEPROM.h>

#define DEFAULT_I2C_ADDRESS 0x08  //!< Default I2C address of the client
#define EEPROM_I2C_ADDRESS 0      //!< EEPROM address for storing the I2C address
#define NEOPIXEL_PIN 4            //!< Data pin for the NeoPixel LED
#define NUMPIXELS 1               //!< Number of LEDs
#define STBY 7                    //!< Standby pin
#define ANALOG_PIN A0             //!< Pin for analogRead
#define TOUCH_PIN 2               //!< Signal from the touch controller when the button is touched
#define INTERRUPT 8               //!< Pin opposite to TOUCH_PIN
#define PWM_PIN 3                 //!< Pin for PWM signal
#define DIR_PIN1 9                //!< Pin for motor direction
#define DIR_PIN2 10               //!< Pin for motor direction
#define OPTIO_PIN 11              //!< Optional IO pin

Adafruit_NeoPixel pixels(NUMPIXELS, NEOPIXEL_PIN, NEO_GRB + NEO_KHZ800);

// Register addresses
enum Register {
  REGISTER_ON = 0,          //!< Register for turning the LED on or off
  REGISTER_RED,             //!< Register for setting the red color value
  REGISTER_GREEN,           //!< Register for setting the green color value
  REGISTER_BLUE,            //!< Register for setting the blue color value
  REGISTER_BRIGHTNESS,      //!< Register for setting the brightness value
  REGISTER_ANALOG_VALUE,    //!< Register for reading the analog value
  REGISTER_TOUCH,           //!< Register for reading the touch state
  REGISTER_OPTIO_READ,      //!< Register for reading the state of OPTIO_PIN
  REGISTER_SET_POSITION,    //!< Register for setting the target position of the servo
  REGISTER_COUNT            //!< Total number of registers
};

// Function declarations
void setLED();
void receiveEvent(int howMany);
void requestEvent();
void updateAnalogValue();
void stopMotor();
void shortBrake();
void standby();
void rotateMotorClockwise(uint8_t pwm);
void rotateMotorCounterclockwise(uint8_t pwm);
void moveMotorToPosition();

uint8_t registers[REGISTER_COUNT] = { 0,    //!< LED ON OFF 1=ON 0=OFF
                                      0,    //!< LED RED
                                      0,    //!< LED GREEN
                                      0,    //!< LED BLUE
                                      0,    //!< LED Brightness
                                      0,    //!< Initial value for ANALOG_VALUE register
                                      0,    //!< Initial value for TOUCH register
                                      0,    //!< Initial value for OPTIO_READ register
                                      0 };  //!< Initial value for SET_POSITION register

uint8_t i2cAddress;
bool touchOccurred = false; // Flag to determine if a touch has been detected
bool optioOccurred = false; // Flag to determine if an optio event has been detected

void setup() {
  Serial.begin(115200);

  // Load the stored I2C address from the EEPROM
  i2cAddress = EEPROM.read(EEPROM_I2C_ADDRESS);
  if (i2cAddress == 0xFF || i2cAddress < 0x08) {  // No valid address stored or address less than 0x08
    i2cAddress = DEFAULT_I2C_ADDRESS;
  }

  // I2C setup
  Wire.begin(i2cAddress);
  Wire.onReceive(receiveEvent);
  Wire.onRequest(requestEvent);

  // NeoPixel setup
  pixels.begin();
  pixels.setBrightness(255);

  // Initialize the analog pin
  pinMode(ANALOG_PIN, INPUT);

  // Initialize the STBY pin
  pinMode(STBY, OUTPUT);
  digitalWrite(STBY, LOW); // Default state

  // Initialize the TOUCH_PIN and INTERRUPT_PIN
  pinMode(TOUCH_PIN, INPUT);
  pinMode(INTERRUPT, OUTPUT);
  digitalWrite(INTERRUPT, HIGH); // Default value for INTERRUPT_PIN

  // Initialize the PWM_PIN and direction pins
  pinMode(PWM_PIN, OUTPUT);
  pinMode(DIR_PIN1, OUTPUT);
  pinMode(DIR_PIN2, OUTPUT);

  // Initialize the OPTIO_PIN
  pinMode(OPTIO_PIN, INPUT_PULLUP);

  // Default state of the motor
  stopMotor();

  // Display the current I2C address
  Serial.print(F("I2C Addr: 0x"));
  Serial.println(i2cAddress, HEX);

  Serial.println(F("Enter new I2C addr in HEX (e.g., 0x09) and press Enter:"));

  // Turn on the LED to green for 1 second on startup
  pixels.setPixelColor(0, pixels.Color(0, 255, 0)); // Green
  pixels.show();
  delay(1000);
  pixels.setPixelColor(0, pixels.Color(0, 0, 0)); // Off
  pixels.show();
}

void loop() {
  // Regularly update the analog value
  updateAnalogValue();

  // Check the state of the OPTIO_PIN
  if (digitalRead(OPTIO_PIN) == LOW) {
    if (!optioOccurred) {
      registers[REGISTER_OPTIO_READ] = 1;
      optioOccurred = true;
      digitalWrite(INTERRUPT, LOW);
    }
  } else {
    registers[REGISTER_OPTIO_READ] = 0;
  }

  // Check the state of the TOUCH_PIN
  if (digitalRead(TOUCH_PIN) == LOW) {
    if (!touchOccurred) {
      registers[REGISTER_TOUCH] = 1;
      touchOccurred = true;
      digitalWrite(INTERRUPT, LOW);
    }
  }

  if (Serial.available()) {
    String input = Serial.readStringUntil('\n');
    input.trim();  // Remove whitespace and newline characters

    if (input.startsWith("0x")) {
      uint8_t newAddress = strtol(input.c_str(), NULL, 16);
      if (newAddress >= 0x08 && newAddress <= 127) {  // Valid I2C addresses: 0x08-0x7F
        EEPROM.write(EEPROM_I2C_ADDRESS, newAddress);
        Serial.print(F("New I2C Addr: 0x"));
        Serial.println(newAddress, HEX);
        Serial.println(F("Restart Arduino for new addr."));
      } else {
        Serial.println(F("Addr must be 0x08-0x7F."));
      }
    }
  }

  delay(10);  // Update every 10 ms
}

/************************************************************************************/
/*!
@brief Sets the color of the LED based on the values in the registers
@return none
*/
/************************************************************************************/
void setLED() {
  if (registers[REGISTER_ON] == 1) {
    // Calculate the color based on the brightness
    uint8_t green = registers[REGISTER_GREEN];
    uint8_t red = registers[REGISTER_RED];
    uint8_t blue = registers[REGISTER_BLUE];
    uint8_t brightness = registers[REGISTER_BRIGHTNESS];

    // Scale the color values according to the brightness
    red = (red * brightness) / 255;
    green = (green * brightness) / 255;
    blue = (blue * brightness) / 255;

    pixels.setPixelColor(0, pixels.Color(green, red, blue));
    pixels.show();
  } else {
    pixels.setPixelColor(0, pixels.Color(0, 0, 0));
    pixels.show();
  }
}

/************************************************************************************/
/*!
@brief Processes the received I2C data
@param howMany Number of received bytes
@return none
*/
/************************************************************************************/
void receiveEvent(int howMany) {
  if (howMany < 2) return;  // Expect at least 2 bytes: register address and value

  uint8_t reg = Wire.read();
  if (reg < REGISTER_COUNT) {
    uint8_t value = Wire.read();
    registers[reg] = value;
    setLED();  // Set the LED after each register update

    // Only move motor when REGISTER_SET_POSITION is updated
    if (reg == REGISTER_SET_POSITION) {
      moveMotorToPosition();
    }
  }
}

/************************************************************************************/
/*!
@brief Processes the I2C data requests
@return none
*/
/************************************************************************************/
void requestEvent() {
  uint8_t reg = Wire.read();
  if (reg < REGISTER_COUNT) {
    Wire.write(registers[reg]);
    
    if (reg == REGISTER_ANALOG_VALUE && touchOccurred) {
      // Set TOUCH register to 0 after ANALOG_VALUE has been read
      registers[REGISTER_TOUCH] = 0;
      touchOccurred = false;
    }

    if (reg == REGISTER_OPTIO_READ && optioOccurred) {
      // Set OPTIO_READ register to 0 after it has been read
      registers[REGISTER_OPTIO_READ] = 0;
      optioOccurred = false;
    }

    // Reset the interrupt pin if no events are pending
    if (!touchOccurred && !optioOccurred) {
      digitalWrite(INTERRUPT, HIGH);
    }
  }
}

/************************************************************************************/
/*!
@brief Updates the value of the analog input and stores it in the corresponding register
@return none
*/
/************************************************************************************/
void updateAnalogValue() {
  uint16_t analogValue = analogRead(ANALOG_PIN);
  registers[REGISTER_ANALOG_VALUE] = map(analogValue, 0, 1023, 0, 255);
}

/************************************************************************************/
/*!
@brief Stops the motor by first applying a short brake, then switching to standby
@return none
*/
/************************************************************************************/
void stopMotor() {
  shortBrake();
  standby();
}

/************************************************************************************/
/*!
@brief Applies a short brake by setting both direction pins to HIGH and the PWM signal to 255
@return none
*/
/************************************************************************************/
void shortBrake() {
  digitalWrite(DIR_PIN1, HIGH);
  digitalWrite(DIR_PIN2, HIGH);
  analogWrite(PWM_PIN, 255);
  digitalWrite(STBY, HIGH);
}

/************************************************************************************/
/*!
@brief Sets the motor to standby by setting both direction pins and the PWM signal to LOW
@return none
*/
/************************************************************************************/
void standby() {
  digitalWrite(DIR_PIN1, LOW);
  digitalWrite(DIR_PIN2, LOW);
  analogWrite(PWM_PIN, 0);
  digitalWrite(STBY, LOW);
}

/************************************************************************************/
/*!
@brief Rotates the motor clockwise by setting DIR_PIN1 to HIGH, DIR_PIN2 to LOW, and setting the PWM signal to the specified value
@param pwm The PWM value to set (0-255)
@return none
*/
/************************************************************************************/
void rotateMotorClockwise(uint8_t pwm) {
  digitalWrite(DIR_PIN1, HIGH);
  digitalWrite(DIR_PIN2, LOW);
  analogWrite(PWM_PIN, pwm);
  digitalWrite(STBY, HIGH);
}

/************************************************************************************/
/*!
@brief Rotates the motor counterclockwise by setting DIR_PIN1 to LOW, DIR_PIN2 to HIGH, and setting the PWM signal to the specified value
@param pwm The PWM value to set (0-255)
@return none
*/
/************************************************************************************/
void rotateMotorCounterclockwise(uint8_t pwm) {
  digitalWrite(DIR_PIN1, LOW);
  digitalWrite(DIR_PIN2, HIGH);
  analogWrite(PWM_PIN, pwm);
  digitalWrite(STBY, HIGH);
}

/************************************************************************************/
/*!
@brief Moves the motor to the position specified in REGISTER_SET_POSITION
@return none
*/
/************************************************************************************/
void moveMotorToPosition() {
  uint8_t targetPosition = registers[REGISTER_SET_POSITION];
  uint8_t currentPosition = registers[REGISTER_ANALOG_VALUE];
  uint8_t pwm = 0;

  while (currentPosition != targetPosition) {
    currentPosition = registers[REGISTER_ANALOG_VALUE];
    int16_t difference = targetPosition - currentPosition;
    if (abs(difference) > 30) {
      pwm = 255;  // Full speed
    } else if (abs(difference) > 10) {
      pwm = 128;  // Medium speed
    } else {
      pwm = 64;  // Low speed
    }

    if (currentPosition < targetPosition) {
      rotateMotorClockwise(pwm);
    } else if (currentPosition > targetPosition) {
      rotateMotorCounterclockwise(pwm);
    }

    updateAnalogValue();
  }

  stopMotor();
}

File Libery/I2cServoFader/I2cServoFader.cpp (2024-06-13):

#include "I2cServoFader.h"

I2cServoFader::I2cServoFader(uint8_t i2cAddress) {
    _i2cAddress = i2cAddress;
}

void I2cServoFader::begin() {
    Wire.begin();
}

void I2cServoFader::setLedColor(uint8_t red, uint8_t green, uint8_t blue) {
    setRegister(REGISTER_RED, red);
    setRegister(REGISTER_GREEN, green);
    setRegister(REGISTER_BLUE, blue);
}

void I2cServoFader::setLedBrightness(uint8_t brightness) {
    setRegister(REGISTER_BRIGHTNESS, brightness);
}

void I2cServoFader::setLedState(bool on) {
    setRegister(REGISTER_ON, on ? 1 : 0);
}

void I2cServoFader::setRegister(Register reg, uint8_t value) {
    Wire.beginTransmission(_i2cAddress);
    Wire.write(static_cast<uint8_t>(reg));
    Wire.write(value);
    Wire.endTransmission();
}

uint8_t I2cServoFader::readRegister(Register reg) {
    Wire.beginTransmission(_i2cAddress);
    Wire.write(static_cast<uint8_t>(reg));
    Wire.endTransmission();
    
    Wire.requestFrom(static_cast<int>(_i2cAddress), static_cast<int>(1));
    if (Wire.available()) {
        return Wire.read();
    }
    return 0; // Return 0 if no value was read
}

uint8_t I2cServoFader::readAnalogValue() {
    return readRegister(REGISTER_ANALOG_VALUE);
}

uint8_t I2cServoFader::readTouch() {
    return readRegister(REGISTER_TOUCH);
}

uint8_t I2cServoFader::readOptio() {
    return readRegister(REGISTER_OPTIO_READ);
}

void I2cServoFader::setPosition(uint8_t position) {
    setRegister(REGISTER_SET_POSITION, position);
}

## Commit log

2024-06-11 0.1
    Noch ohne Motoransteuerung Beta
2024-06-12 Update PCB auf 1.0
    [MotorFaderTB6612.V.1.0.brd, MotorFaderTB6612.V.1.0.sch]
2024-06-12 Dateinamen gändert
    [ServoFaderTB6612.V.1.0.brd, ServoFaderTB6612.V.1.0.sch]
2024-06-12 Add STBY Pin
2024-06-12 Update Pin PB3
    [ServoFaderTB6612.V.1.0.brd, ServoFaderTB6612.V.1.0.sch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]
2024-06-13 Update
    Motorsteuerung mit ABS eingefügt
    [ServoFaderTB6612.V.1.0.brd, ServoFaderTB6612.V.1.0.sch]
